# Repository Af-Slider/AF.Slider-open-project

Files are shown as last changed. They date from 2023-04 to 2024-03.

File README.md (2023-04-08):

# AF.Slider-open-project
Open source motorized camera slider, all partes are 3D printable or easy to find on the market. 
Latest version of AF.Slider 21.3

In this repo you can find all the data, files, CAD and scripts used on AF.Slider products. It's distributed under Creative Commons NonCommercial license: feel free to modify and/or change any aspect of the slider, as long as it is used for personal purposes only, without the possibility of it being redistributed or resold. The design of the slider is protected by European Community Design Rights – unregistered Community design (UCD).

<!DOCTYPE html>

<a rel="license" href="http://creativecommons.org/licenses/by-nc-sa/4.0/">

Slider_cover

Here you can find the complete BOM for the slider, together with a sourcing list:

  BOM - https://docs.google.com/spreadsheets/d/e/2PACX-1vTk2jxu348yVe4P4dr0VMHoAVMZ_PHeQANC6IF_kKDuW8Oi32bRA98299qZgVoONA/pubhtml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
  
  Sorucing List - https://docs.google.com/spreadsheets/d/e/2PACX-1vTk2jxu348yVe4P4dr0VMHoAVMZ_PHeQANC6IF_kKDuW8Oi32bRA98299qZgVoONA/pubhtml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

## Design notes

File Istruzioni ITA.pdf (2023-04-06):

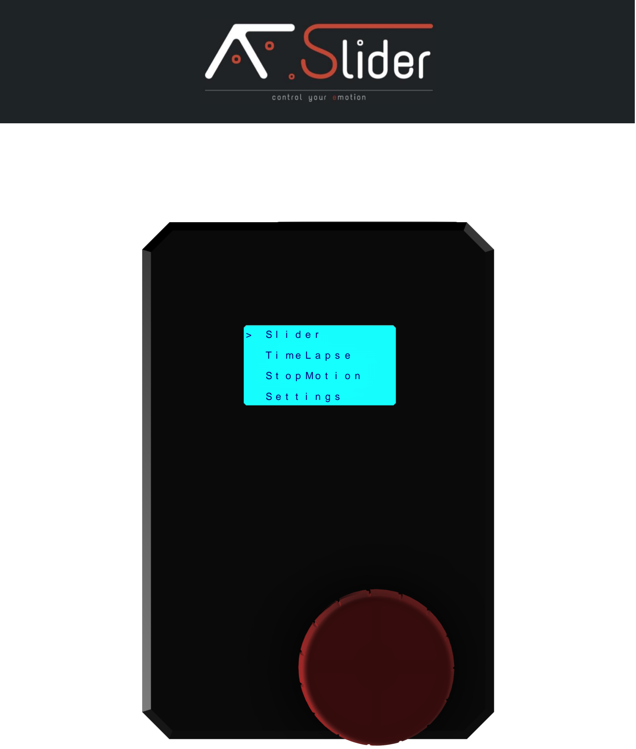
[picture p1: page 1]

> | S l i d e r
| T i m e L a p s e
| S t o p M o t i o n
| S e t t i n g s

# Istruzioni

### Sommario

Componenti dello slider | 3
Primo avvio | 4
Alimentazione | 4
Menu principale | 5
Slider | 5
TimeLapse | 6
StopMotion | 6
Settings | 7
Funzioni Generali | 8
Homing | 8
Firmware Update | 8
Bluetooth e App | 10
Sostituzione dei binari | 11

# Componenti dello slider

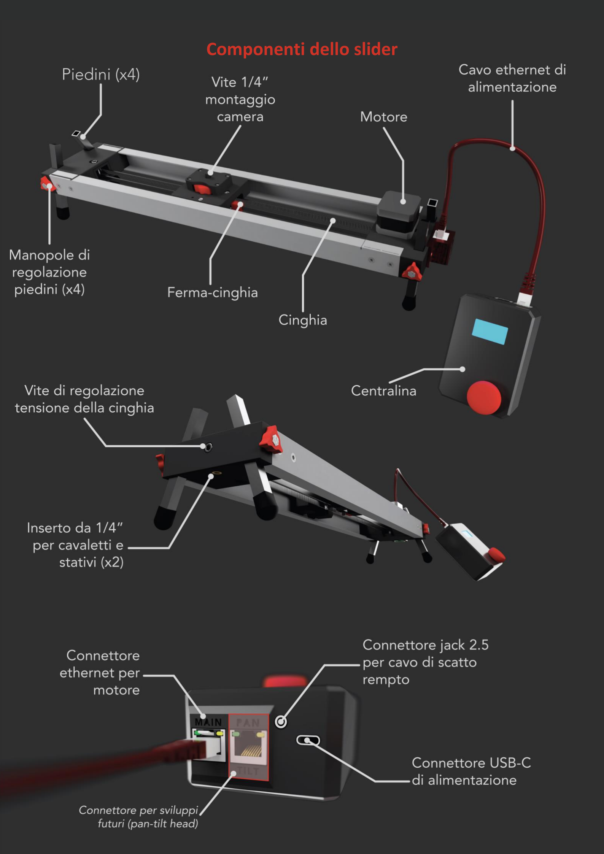
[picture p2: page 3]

# Primo avvio

Prima di avviare lo slider è bene conoscere come connettere correttamente i diversi cavi. All’interno della confezione troverete:
- Un cavo ethernet
- Un cavo USB type-C
- Un alimentatore USB type-C Power Delivery da muro

Cavo USB type-C
Il cavo USB type-C è utilizzato per alimentare lo slider. Connetterlo all’alimentatore fornito in dotazione, o ad altri con caratteristiche simili. È possibile inoltre alimentare lo slider con powerbank purché dotati di presa USB type-C è di tecnologia Power Delivery (per erogare 12V).

Cavo Ethernet
Il cavo ethernet è utilizzato per portare l’alimentazione dalla centralina al motore.
N.B. Assicuratevi di connettere il cavo ethernet alla porta corretta, cioè la porta sulla centralina con dicitura “MAIN”.

N.B. Prima di connettere il cavo di alimentazione dello slider, verificare che il cavo ethernet del motore sia connesso!

Ad ogni accensione lo slider esegue una rapida procedura di calibrazione, cioè verifica la lunghezza dei binari e la posizione di partenza (“HOME”). Durante la procedura di calibrazione, sullo schermo della centralina compare la scritta “homing”. Al termine della procedura, è possibile iniziare ad utilizzare lo slider. Se la procedura di calibrazione non dovesse andare a buon fine, è possibile eseguirla nuovamente dal menu “settings” (vedi capitolo dedicato). N.B. Per garantire la riuscita della procedura di calibrazione, è bene che essa venga eseguita a slider “scarico”, cioè senza che la camera da presa sia montata su di esso.

Cavo jack 2.5” – scatto remoto
Il cavo di scatto remoto deve essere acquistato separatamente e deve essere scelto in base alla camera che verrà utilizzata; il circuito di controllo all’interno della camera infatti è differente per ogni marchio (es. Lumix, SONY, Canon, Nikon, Fujifilm, etc.).
N.B. Per poter utilizzare la funzione di scatto remoto, la camera da presa deve essere impostata su “messa a fuoco manuale”.
Connettere il cavo di scatto remoto con il jack da 3 poli all’interno dell’apposita presa sulla centralina e l’altro capo nel connettore della camera da presa.

# Alimentazione

Per alimentare correttamente lo slider, è bene utilizzare l’alimentatore fornito in dotazione o alimentatori/powerbank con caratteristiche simili:
- Presa USB type-C
- Tecnologia Power Delivery (output 5V, 9V, 12 V)
- 15 W di potenza minima in uscita
Se alimentando lo slider con alimentatori e/o powerbank differenti notate malfunzionamenti o un calo nella forza esercitata dal motore, verificate che l’alimentazione che state utilizzando sia corretta.

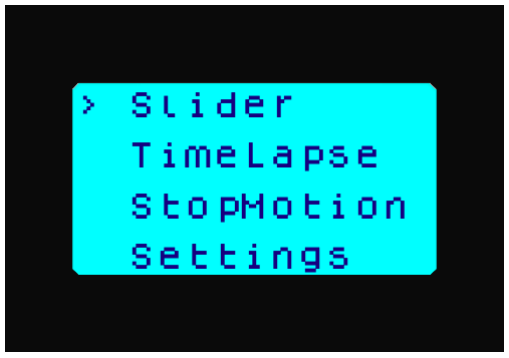
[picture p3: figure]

# Menu principale

Seleziona una delle funzioni presenti per entrare nel sotto-menu relativo.
Per muoversi all’interno del menu, rotare in senso orario o antiorario la manopola presente sulla centralina.
In tutti i menu sono presenti due tipi di cursore:
> | Indica la voce su cui è posizionato il selettore
* | Indica che è stata selezionata la voce ed è possibile modificarne il valore ruotando la manopola

## Slider

Funzione base per poter muovere lo slider con movimento continuo. Ogni cambio di movimento (partenza, stop, ripartenza, etc.) sarà accompagnato da una graduale accelerazione/decelerazione, in base al valore impostato. Di default alla fine del loop lo slider ripeterà il movimento in direzione opposta a ciclo continuo. Per modificare questo parametro vedi il sotto-menu “Settings”.

Speed | velocità a cui si muoverà lo slider (in mm/s)

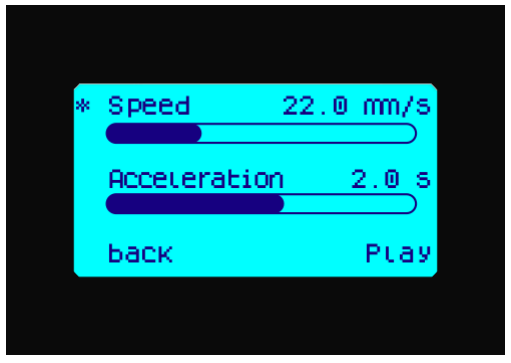
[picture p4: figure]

Acceleration | tempo in secondi che lo slider impiegherà per raggiungere la velocità impostata

## TimeLapse

Permette di muovere lo slider in modo discontinuo e automatico per realizzare timelapse. La camera può essere collegata alla centralina tramite apposito cavo; ad ogni step la centralina muoverà il carrello dello step impostato ed invierà alla camera il comando di scatto remoto. Arrivato a fine corsa lo slider ripeterà la corsa in direzione opposta a ciclo continuo.
Per modificare questo parametro vedi il sotto-menu “Settings”.
Step | Spostamento eseguito ad ogni scatto.

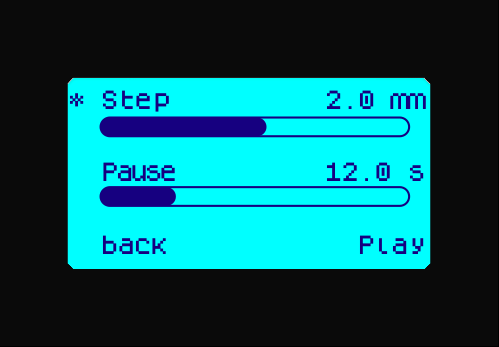
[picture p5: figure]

Pausa | tempo in secondi che lo slider farà intercorrere fra uno scatto ed il successivo
N.B.
La camera deve essere impostata su messa a fuoco manuale per poter scattare in remoto

## StopMotion

Simile alla funzione TimeLapse, ma il movimento ad ogni step avviene solo dopo aver ricevuto il comando dell’operatore. Se la camera è collegata, ad ogni step verrà inviato il comando di scatto remoto. È possibile avanzare ed arretrare di uno step alla volta per eseguito un nuovo scatto o per ripetere il precedente. Arrivato a fine corsa lo slider ripeterà la corsa in direzione opposta a ciclo continuo. Per modificare questo parametro vedi il sotto-menu “Settings”.
N.B.
La camera deve essere impostata su messa a fuoco manuale per poter scattare in remoto

Menu parametri
Step Spostamento eseguito ad ogni scatto.

Menu Play
Next | Esegue uno spostamento in avanti (in direzione del movimento corrente) ed invia il
| comando di scatto remoto alla camera

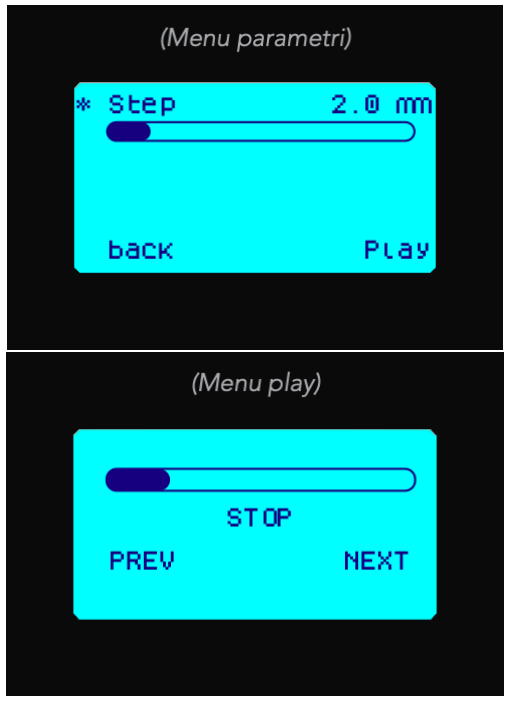
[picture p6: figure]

Prev | Esegue uno spostamento indietro (in direzione opposta al movimento corrente) ed invia il
| comando di scatto remoto alla camera

# Settings

All’interno di questo sotto-menu è possibile cambiare alcune impostazioni generali ed eseguire operazioni particolari:

Impostazione parametri:

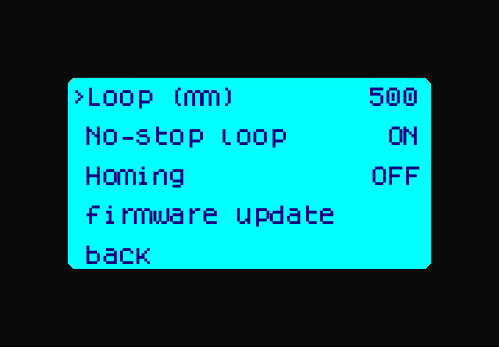
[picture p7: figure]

Loop | Imposta la lunghezza della corsa che deve eseguire lo slider. Di default viene riportata la lunghezza misurata all’avvio dello slider (vedi “homing”). Modificando questo parametro è possibile accorciare la corsa che lo slider esegue per ogni ciclo.
No-stop loop | Se impostato su “ON”, lo slider esegue la corsa in modo continuo “andata” e “ritorno”, senza mai fermarsi. Se impostato su “OFF”, una volta arrivato a fine corsa lo slider si fermerà automaticamente.

Operazioni eccezionali:

Homing | Quando avviato (impostando il valore su “ON”, per evitare di premere accidentalmente la funzione) viene eseguita nuovamente la misurazione dei binari e il posizionamento iniziale (“home”).

Firmware update Permette di aggiornare il firmware. Una volta entrati nel sotto-menu, lo slider
| tenterà di connettersi alla rete Wi-Fi impostata, per registrare l’indirizzo IP a cui effettuare la connessione per eseguire l’aggiornamento. Per eseguire l’aggiornamento vedere la sezione “Firmware Update”.

# Funzioni Generali

### Homing

All’avvio dello slider viene eseguita di default per determinare la lunghezza dei binari e la posizione di partenza (definita “home”). Per garantire il corretto funzionamento di questa operazione è bene che sia eseguita a slider “scarico”, cioè senza camera montata su di esso, in particolar modo se l’operazione viene eseguita quando lo slider è in posizione verticale o inclinata.
È possibile eseguire manualmente questa operazione andando nel sotto-menu “Settings”.

Inoltre è possibile riportare in posizione “home” lo slider in qualsiasi momento (purché lo slider sia fermo), tenendo premuta la manopola per più di 2,5 secondi; al rilascio, lo slider tornerà automaticamente in posizione iniziale.

### Firmware Update

È possibile eseguire l’aggiornamento del firmware qualora dov’esse essere rilasciata una nuova versione. Per eseguire l’aggiornamento, è necessario disporre di:
- Un computer
- Uno smartphone in grado di creare un hotspot
- Una connessione ad internet

Una volta scaricato il file dal sito www.afslider.it, eseguire i seguenti passaggi:

1. Creare una rete Wi-Fi hotspot con il proprio smartphone con le seguenti credenziali (rispettando le maiuscole/minuscole)
a. Nome hotspot – Slider_wifi
b. Password hotspot – Afslider
2. Accedere al sotto-menu “firmware update” (“Settings → firmware update”)
3. Attendere la connessione dello slider alla rete appena creata. Una volta che avrà eseguito l’accesso, sulla schermata comparirà una nuova schermata che riporta la versione corrente del firmware installato e l’indirizzo IP acquisito. Copiare l’indirizzo IP riportato nella schermata.

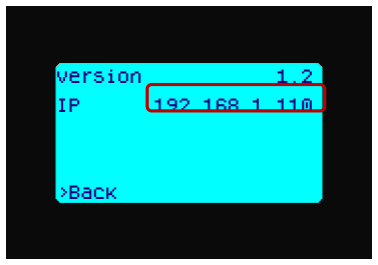
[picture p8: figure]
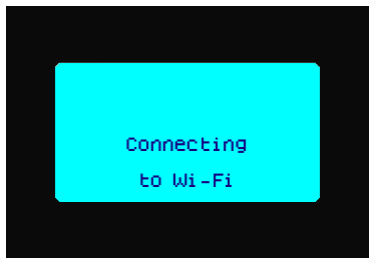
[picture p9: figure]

4. Aprire il browser preferito dal proprio computer (es. Chrome, Firefox, Safari, etc.), ed inserire nella barra di navigazione l’indirizzo IP copiato seguito da “/update”; nell’esempio riportato nell’immagine, verrà digitato -192.168.1.110/update
5. Una volta caricata la schermata, apparirà a schermo la seguente finestra -

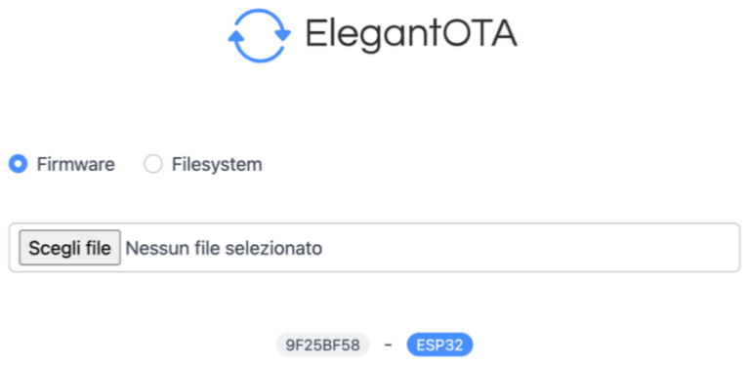
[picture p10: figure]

6. Senza cambiare i parametri già settati di default, selezionare il firmware precedentemente scaricato cliccando su “scegli file”.
7. Il firmware verrà caricato automaticamente. Attendere il completamento della barra di caricamento prima di chiudere la finestra di navigazione.
8. Una volta che l’aggiornamento è stato completato, si noterà che la centralina dello slider si è riavviata. La procedura è quindi conclusa.

Note:
- Se la procedura di upload del firmware allo slider dovesse bloccarsi, spegnere e riaccendere lo slider e ripetere nuovamente la medesima procedura.
- Se dovesse sussisterete il problema, provare ad alimentare la
centralina con un cavo USB-A / USB-C (vedi immagine a lato); così facendo lo slider viene alimentato a 5V anziché a 12V, disattivando alcuni componenti che potrebbero interferire con la procedura di caricamento del firmware.

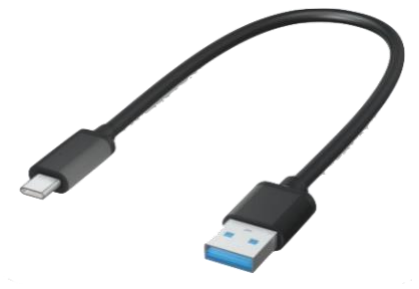
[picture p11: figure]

# Bluetooth e App

Lo slider è già abilitato alla connessione Bluetooth. Su specifica richiesta del cliente è possibile riceve una versione beta dell’applicazione da poter testare. Appena la versione finale dell’applicazione sarà disponibile, tutti gli acquirenti verranno prontamente informati.

Attenzione! La versione beta non garantisce il corretto funzionamento in tutte le circostanze, e può richiedere il riavvio dello slider per ripristinare le funzioni primarie.

# Sostituzione dei binari

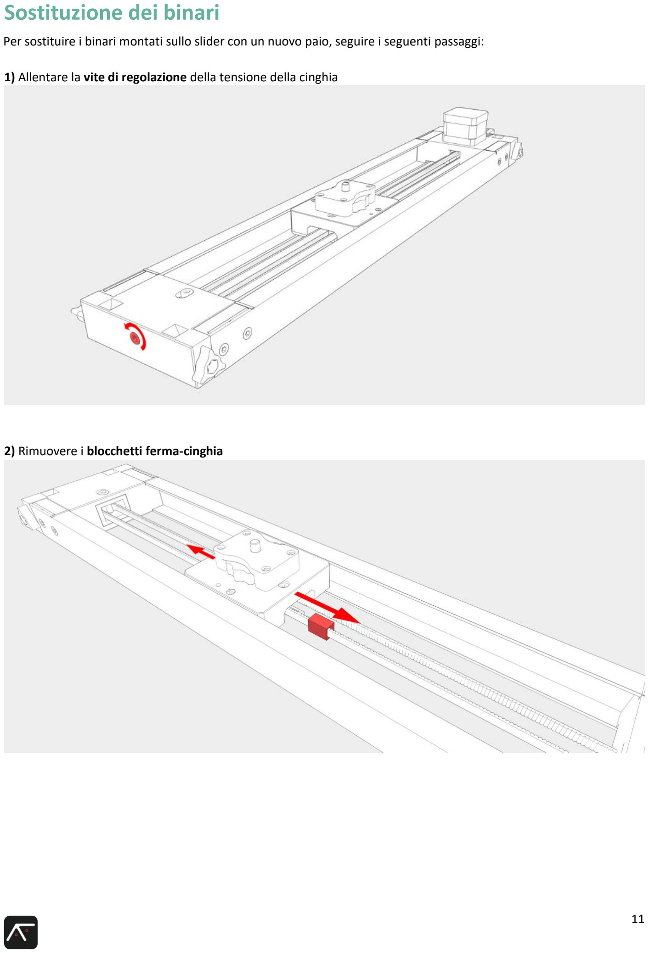
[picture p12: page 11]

Per sostituire i binari montati sullo slider con un nuovo paio, seguire i seguenti passaggi:

1) Allentare la vite di regolazione della tensione della cinghia
2) Rimuovere i blocchetti ferma-cinghia

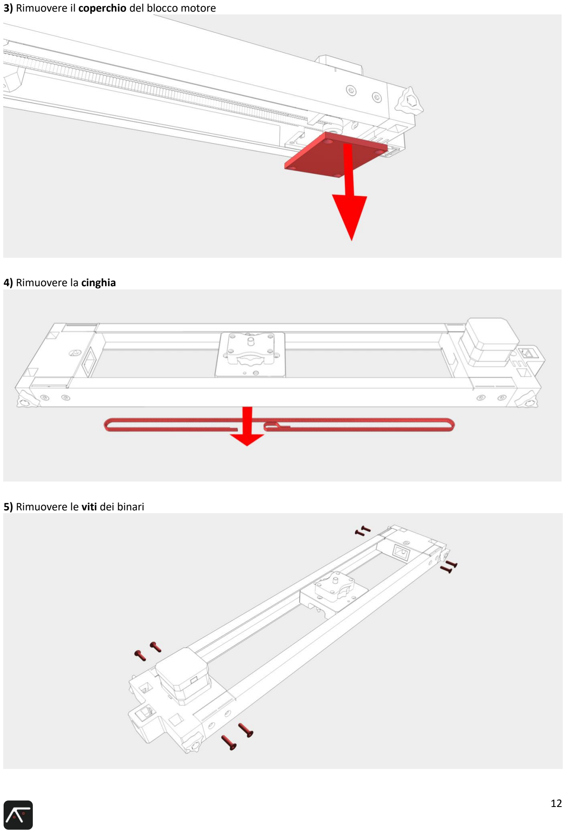
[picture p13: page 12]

3) Rimuovere il coperchio del blocco motore
4) Rimuovere la cinghia
5) Rimuovere le viti dei binari

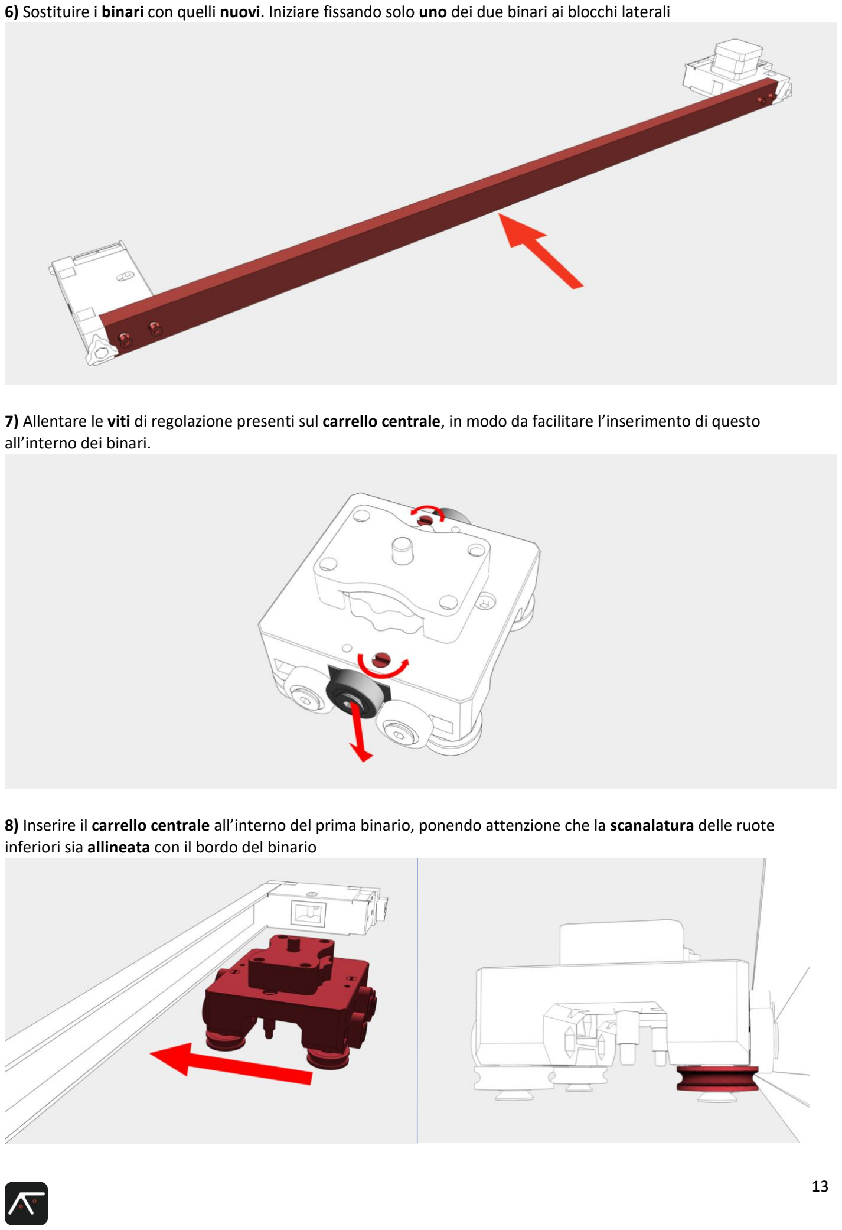
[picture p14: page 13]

6) Sostituire i binari con quelli nuovi. Iniziare fissando solo uno dei due binari ai blocchi laterali
7) Allentare le viti di regolazione presenti sul carrello centrale, in modo da facilitare l’inserimento di questo all’interno dei binari.
8) Inserire il carrello centrale all’interno del prima binario, ponendo attenzione che la scanalatura delle ruote inferiori sia allineata con il bordo del binario

10) Montare il secondo binario, ponendo sempre attenzione che le ruote inferiore del carrello siano ben allineate.

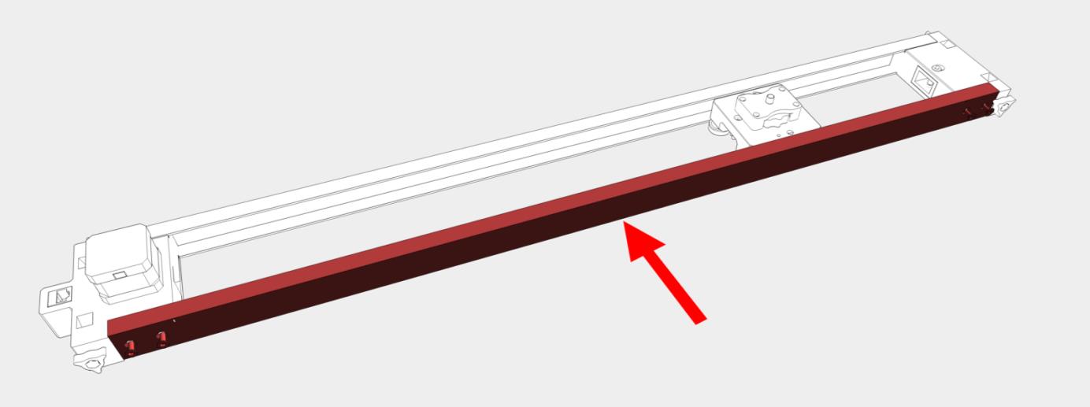
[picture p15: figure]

11) Regolare la posizione delle ruote del carrello centrale con le apposite vite di regolazione. Il carrello deve scorrere senza fare forza, ma senza avere possibilità di muoversi in direzione laterale. Più le viti sono serrate, meno il carrello può muoversi in direzione laterale, ma maggiore sarà la forza richiesta per spostarlo; una forza eccessiva può portare ad un movimento poco fluido del carrello.

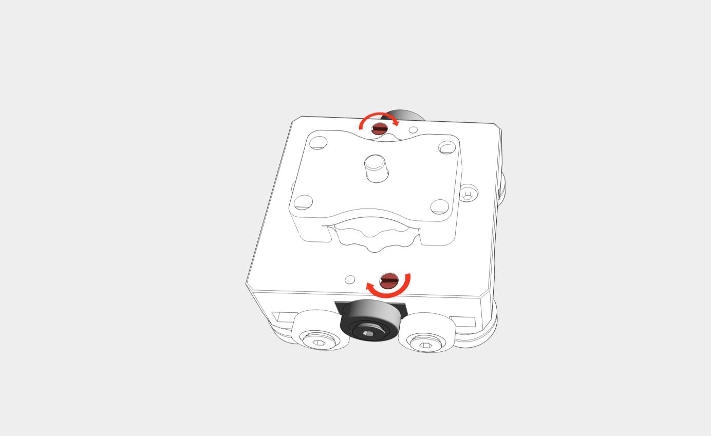
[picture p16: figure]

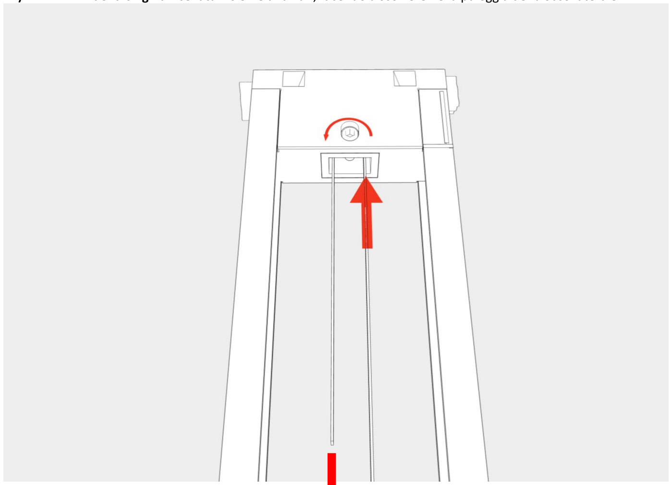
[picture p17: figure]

12) Inserire la nuova cinghia ricevuta insieme ai binari, facendola scorrere nella puleggia del blocco laterale

13) Fissare la cinghia al carrello centrale con i blocchetti ferma-cinghia:
a) Inserire il blocchetto ferma-cinghia sul primo capo della cinghia
b) Fare un’asola attorno al supporto sul carrello centrale con la cinghia stessa
c) Far combaciare le dentature dei due lati opposti della cinghia una volta completata l’asola
d) Far scorrere il blocchetto ferma-cinghia verso l’asola per bloccare la cinghia stessa

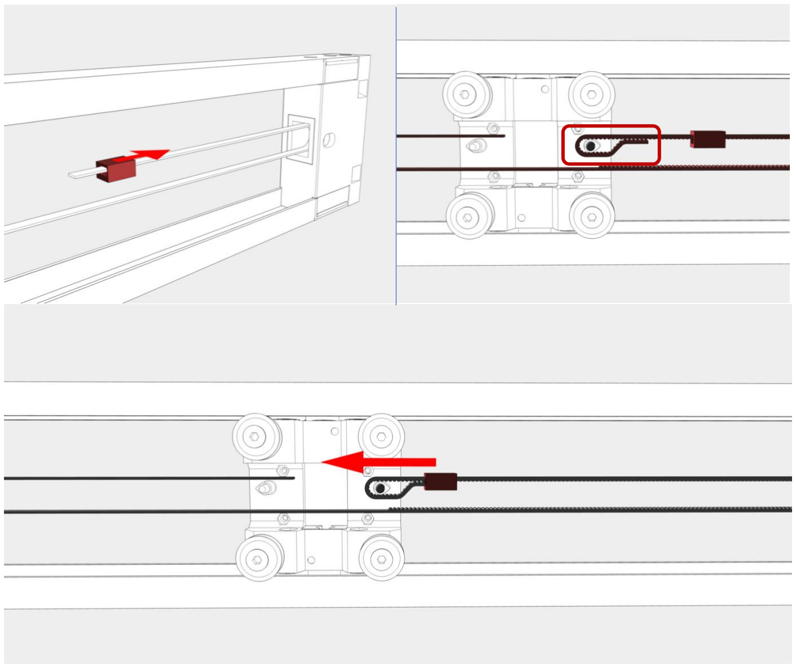
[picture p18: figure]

14) Far scorrere la cinghia attorno alla puleggia del motore

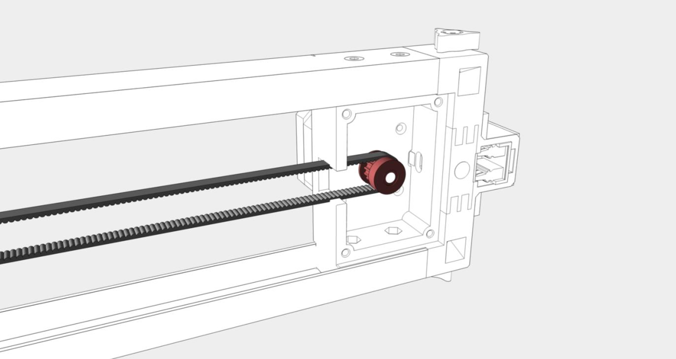
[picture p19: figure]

15) Ripetere le operazioni del passaggio 13 per l’altro capo della cinghia. Prestare attenzione che la cinghia sia sufficientemente tesa prima di fermarla con l’apposito blocchetto ferma-cinghia.
16) Regolare la tensione della cinghia stringendo la vite di regolazione della tensione sul blocco laterale. Verificare che la cinghia non sia troppo tesa facendo scorrere il carrello centrale; se la tensione è corretta si deve sentire una leggera resistenza ma non eccessiva.

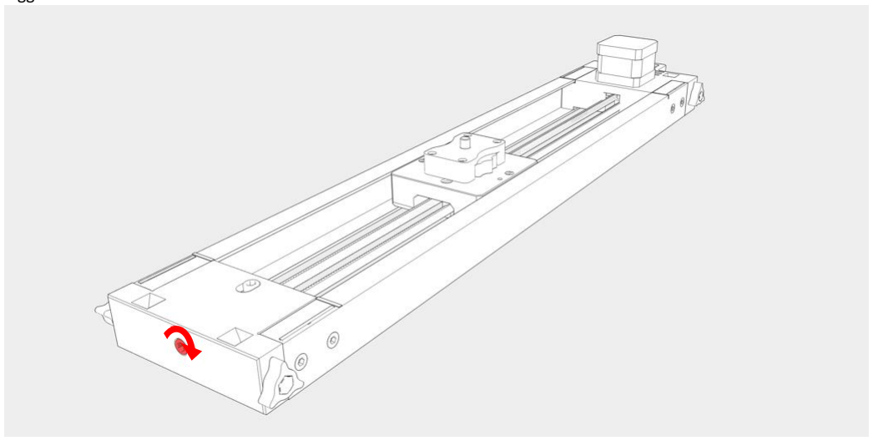
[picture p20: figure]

17) Chiudere il blocco motore con il coperchio.

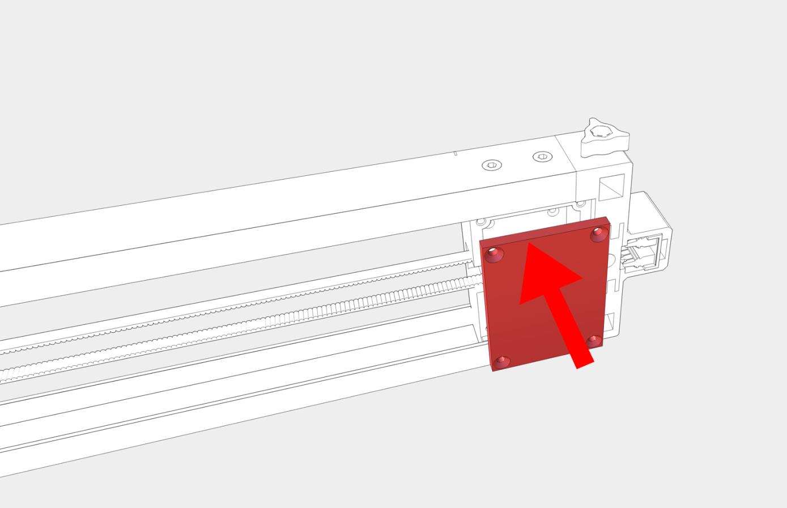
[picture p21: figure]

Avete concluso la procedura! Testate lo slider un paio di volte per verificare che la tensione della cinghia e la posizione delle ruote del carrello centrale sia corretta.

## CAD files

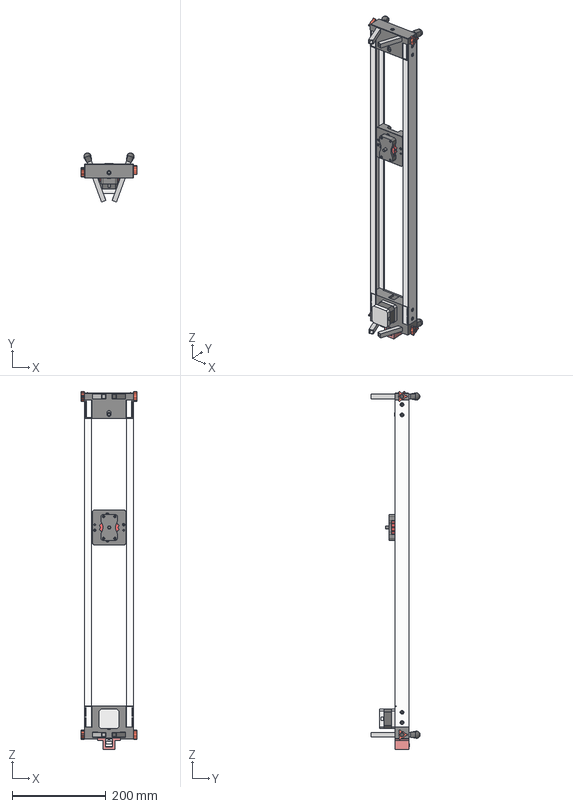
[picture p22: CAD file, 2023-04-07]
CAD/STEP/Assieme Slider V3.4 v84.step
119.8 x 105.1 x 765.7 mm
Profilo_Al x 2
Nema_17_stepper
Coperchio
Keystone_socket_RJ45
T5 Pulley_1
Cuscinetto piatto_crie ruote x 6
Supporto camera V2
Manopola vite 1/4 V2 - wurth
vite 1/4" - 20 x 5/8"
M3 x 6
M5 x 6
M4x 20 svasata x 10
Blocco_laterale
Piedino Al x 4
piedino x 4
M5 Cilindrica x 2
manopola piedini v2 x 4
M5 esagonale x 4
Inserto 1/4"

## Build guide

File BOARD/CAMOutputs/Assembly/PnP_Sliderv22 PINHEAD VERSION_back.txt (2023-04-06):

9V_PAD2	86.11	8.13	180.00		SMD1,27-2,54
GND_PAD2	86.11	3.05	180.00		SMD1,27-2,54

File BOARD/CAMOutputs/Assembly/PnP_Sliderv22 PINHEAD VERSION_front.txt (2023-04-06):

GND	4.83	12.32	90.00		SMD2,54-5,08
PAD1	80.65	3.05	90.00		SMD2,54-5,08
PAD2	80.65	8.13	90.00		SMD2,54-5,08
VCC	4.70	18.41	90.00		SMD2,54-5,08

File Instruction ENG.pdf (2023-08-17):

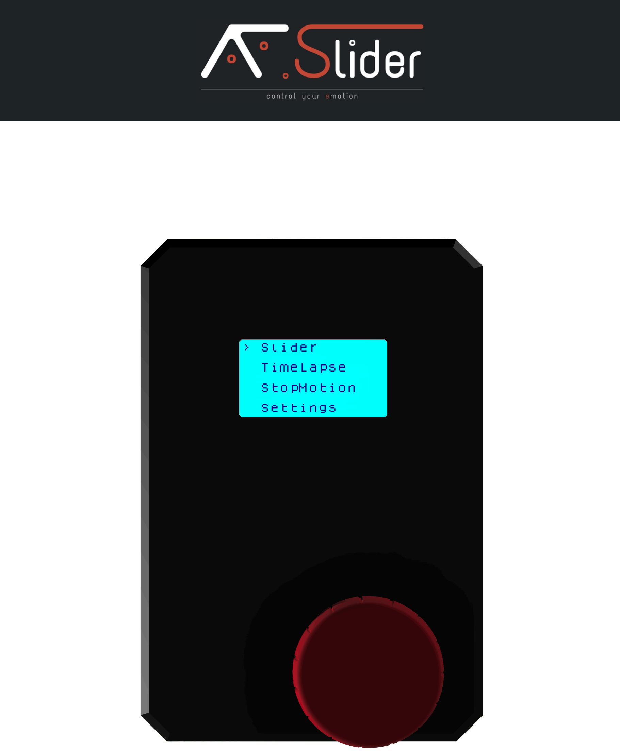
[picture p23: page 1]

> Slider

TimeLapse

StopMotion

Settings

# Instructions

### Summary

Componenti dello slider | 3
Primo avvio | Errore. Il segnalibro non è definito.
Alimentazione | Errore. Il segnalibro non è definito.
Menu principale | 5
Slider | 5
TimeLapse | 6
StopMotion | 6
Settings | 6
Funzioni Generali | 8
Homing | 8
Firmware Update | 8
Bluetooth e App | 10
Sostituzione dei binari | 11

# Slider components

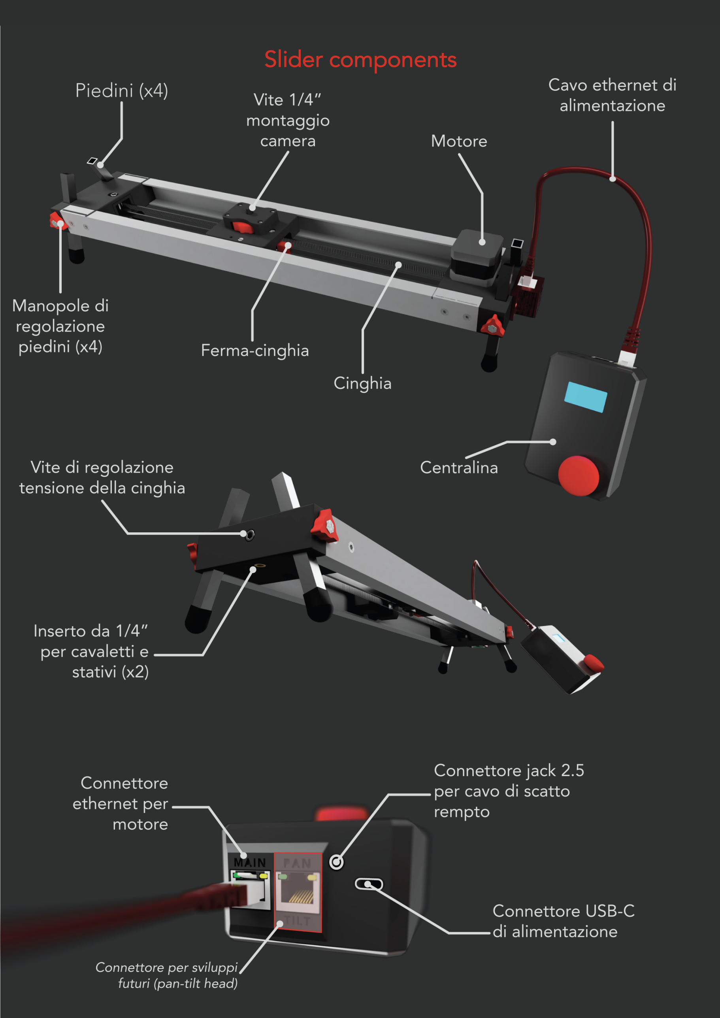
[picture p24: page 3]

# First startup

Before starting the slider, it is good to know how to properly connect the different cables. Inside the package, you will find:
- An Ethernet cable
- A USB Type-C cable
- A USB Type-C Power Delivery wall charger

USB type-C cable
The USB Type-C cable is used to power the slider. Connect it to the provided wall charger or other similar chargers. It is also possible to power the slider with a power bank as long as it has a USB Type-C port and Power Delivery technology (to deliver 12V).

Ethernet cable
The Ethernet cable is used to supply power from the controller to the motor. Note: Make sure to connect the Ethernet cable to the correct port, which is the one labeled "MAIN" on the controller.

Note: Before connecting the power cable to the slider, make sure that the motor's Ethernet cable is connected!

During each power-on, the slider performs a quick calibration procedure to verify the length of the rails and the starting position ("HOME"). During the calibration procedure, the "homing" message appears on the controller's screen. Once the procedure is completed, you can start using the slider. If the calibration procedure fails, you can perform it again from the "settings" menu (refer to the dedicated chapter). Note: To ensure a successful calibration procedure, it is recommended to perform it with the slider "unloaded," meaning without the camera mounted on it.

jack 2.5” Cable – remote shutter

The remote shutter cable needs to be purchased separately and should be chosen based on the camera that will be used. The control circuit inside the camera varies for each brand (e.g., Lumix, SONY, Canon, Nikon, Fujifilm, etc.).
Note: To use the remote shutter function, the camera must be set to "manual focus" mode. Connect the remote shutter cable with the 3-pole jack into the dedicated socket on the controller, and the other end into the camera's connector.

# Power Supply

To properly power the slider, it is recommended to use the provided power adapter or power supplies/power banks with similar specifications:
- USB Type-C port
- Power Delivery technology (output 5V, 9V, 12V)
- Minimum 15W power output
If you experience malfunctions or a decrease in motor force when using different power supplies or power banks, verify that the power source you are using is correct.

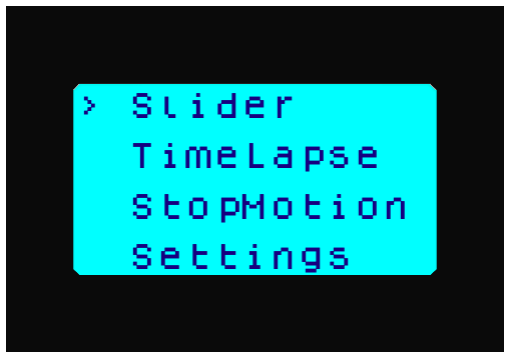
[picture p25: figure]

# Main Menu

Choose one of the available functions to access the corresponding submenu. To navigate within the menu, rotate the dial on the controller clockwise or counterclockwise. In all menus, you will find two types of cursors.

> | It indicate the option on which the selector is positioned
* | It indicates that the option has been selected, and the value can be modified by rotating the dial

## Slider

The basic function that allows you to move the slider with continuous motion. Each change of motion (start, stop, restart, etc.) will be accompanied by a gradual acceleration/deceleration, based on the set value. By default, at the end of the loop, the slider will repeat the movement in the opposite direction in a continuous cycle. To modify this parameter, please refer to the "Settings" submenu.

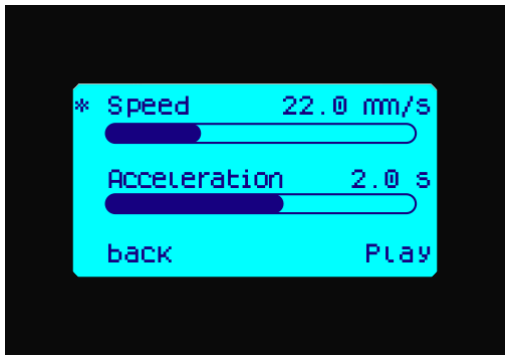
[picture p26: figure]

Speed The speed at which the slider will move is measured in mm/s (millimeters per second).

Acceleration The time in seconds that the slider will take to reach the set speed

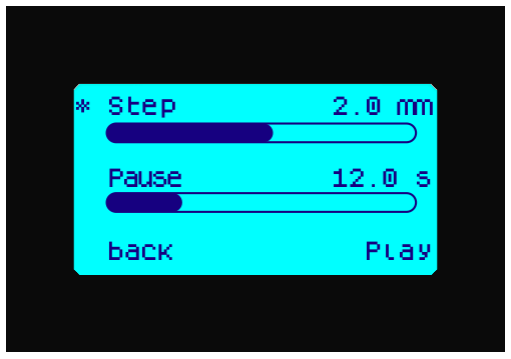
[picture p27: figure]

## TimeLapse

Allows you to move the slider in a discontinuous and automatic manner to create timelapse sequences. The camera can be connected to the controller using a dedicated cable. At each step, the controller will move the slider by the set step distance and send a remote shutter command to the camera. Once it reaches the end of the rail, the slider will repeat the movement in the opposite direction in a continuous cycle. To modify this parameter, refer to the "Settings" submenu.

Step movement that will be performed at each step
Pausa time in second between each step
N.B.
The camera needs to be set to manual focus in order to take remote shots.

## StopMotion

Similar to the TimeLapse function, but the movement at each step occurs only after receiving the command from the operator. If the camera is connected, a remote shutter command will be sent at each step. It is possible to move forward and backward one step at a time to take a new shot or repeat the previous one. Once it reaches the end of the rail, the slider will repeat the movement in the opposite direction in a continuous cycle. To modify this parameter, refer to the "Settings" submenu.

N.B.
The camera needs to be set to manual focus in order to take remote shots.

Parameters Menu
Step movement that will be performed at each step

Menu Play

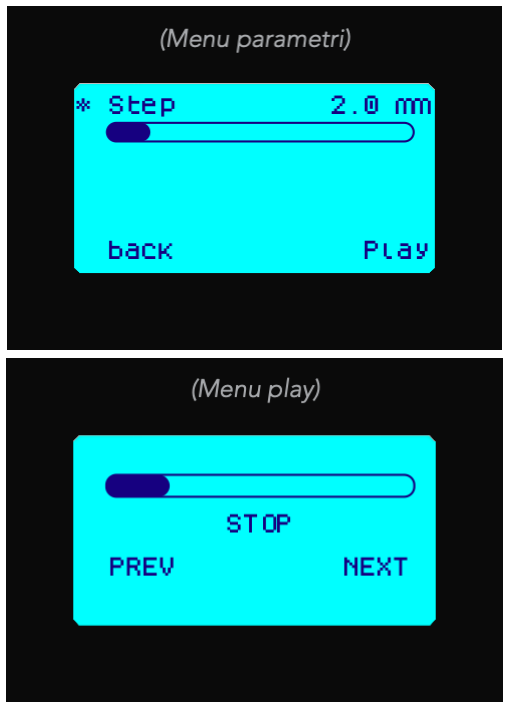
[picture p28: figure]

Next | It performs a forward movement (in the direction of the current motion) and sends the remote
| shutter command to the camera.
Prev | It performs a backward movement (in the opposite direction of the current motion) and sends the
| remote shutter command to the camera.

Settings
Within this submenu, you can change some general settings and perform specific operations.

Parameters set:


Loop | Set the length of the travel that the slider should perform. By default, it displays the length measured during the slider's initialization (refer to "homing"). By modifying this parameter, you can shorten the travel distance that the slider completes in each cycle.
No-stop loop | If set to "ON", the slider will continuously move back and forth without ever stopping. If set to "OFF", once it reaches the end of the rail, the slider will automatically stop.

Exceptional operations:

Homing | When started (by setting the value to "ON" to avoid accidentally triggering the function), the measurement of the rails and the initial positioning ("home") is performed again.
Firmware update | It allows you to update the firmware. Once you enter the submenu, the slider will attempt to connect to the set Wi-Fi network to record the IP address for the connection to perform the update. To carry out the update, refer to the "Firmware Update" section.

# General Functions

### Homing

By default, when the slider is powered on, it performs a calibration procedure to determine the rail length and the starting position, referred to as "home." To ensure the proper functioning of this operation, it is recommended to perform it with the slider "unloaded," meaning without a camera mounted on it, especially if the operation is carried out when the slider is in a vertical or tilted position.
You can manually execute this operation by accessing the "Settings" submenu.
Additionally, it is possible to return the slider to the "home" position at any time (as long as the slider is stationary) by pressing and holding the dial for more than 2.5 seconds. Upon release, the slider will automatically return to its initial position.

### Firmware Update

You can update the firmware if a new version is released. To perform the update, you will need:

- A computer
- A smartphone capable of creating a hotspot
- An internet connection

Once you have downloaded the file from the website www.afslider.it, follow these steps:

1. Create a Wi-Fi hotspot network with your smartphone using the following credentials (pay attention to uppercase/lowercase letters):
a. Hotspot name – Slider_wifi
b. Hotspot password – Afslider
2. Access the "firmware update" submenu ("Settings → firmware update").
3. Wait for the slider to connect to the newly created network. Once it has successfully connected, a new screen will appear displaying the current installed firmware version and the acquired IP address. Copy the displayed IP address.

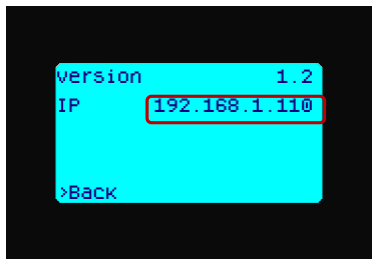
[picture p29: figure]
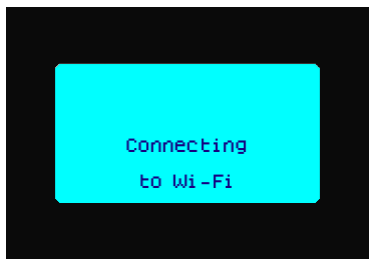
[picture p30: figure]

4. Open your preferred browser on your computer (e.g., Chrome, Firefox, Safari, etc.) and enter the copied IP address followed by "/update" in the navigation bar. In the example shown in the image, it would be typed as -

192.168.1.110/update

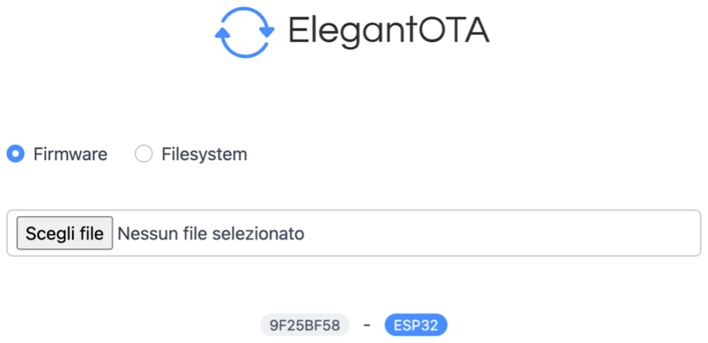
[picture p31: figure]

5. Once the screen is loaded, the following window will appear on the screen.
6. Without changing the default settings, select the previously downloaded firmware by clicking on "choose file."
7. The firmware will be automatically uploaded. Wait for the progress bar to complete before closing the browser window.
8. Once the update is completed, you will notice that the slider's controller has restarted. The procedure is now complete.

Note:
- If the firmware upload process to the slider gets stuck, turn off and restart the slider, then repeat the same procedure.
- If the issue persists, try powering the controller with a USB-A
to USB-C cable (as shown in the image). By doing so, the slider is powered at 5V instead of 12V, deactivating some components that might interfere with the firmware upload process.

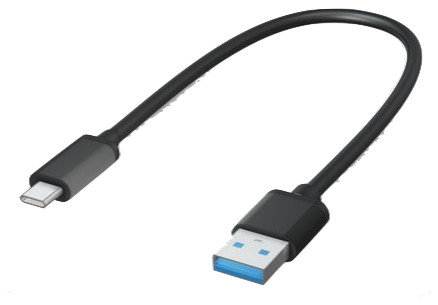
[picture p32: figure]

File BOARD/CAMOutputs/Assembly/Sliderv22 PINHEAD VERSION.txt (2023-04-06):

Partlist exported from /Users/fulvio_airaghi/Documents/EAGLE/projects/Test_project/Sliderv22 PINHEAD VERSION.sch at 07/10/22 12:50

Qty Value          Device                Package      Parts                                Description                     DATASHEET                                                                                                                                                          MANUFACTURER    MF                      MPN  OC_FARNELL OC_NEWARK PARTREV POPULARITY SPICEPREFIX STANDARD                    
6                  1,6/0,8               1,6/0,8      PAD3, PAD6, PAD8, PAD9, PAD12, PAD13 THROUGH-HOLE PAD                                                                                                                                                                                                                                                             15                                                 
2                  2,54/1,0              2,54/1,0     9V_PAD, GND_PAD                      THROUGH-HOLE PAD                                                                                                                                                                                                                                                             1                                                  
1                  FE04-1FE-04-1         FE04-1       SV9                                  FEMALE HEADER                                                                                                                                                                                                                                                                                                                   
3                  FE08-TMC2209-DXFE8-DX FE08-DX      SV1, SV5, SV7                        FEMALE HEADER                                                                                                                                                                                                                                                                                                                   
3                  FE08-TMC2209-SX       FE08-SX      SV4, SV6, SV8                        FEMALE HEADER                                                                                                                                                                                                                                   unknown    unknown           10                                                 
1                  FE15-1-ESP32-DX       FE15-DX      SV3                                  FEMALE HEADER                                                                                                                                                                                                                                                                                                                   
1                  FE15-1-ESP32-SX       FE15-SX      SV2                                  FEMALE HEADER                                                                                                                                                                                                                                                                                                                   
2                  SMD2                  SMD1,27-2,54 9V_PAD2, GND_PAD2                    SMD PAD                                                                                                                                                                                                                                                                      15                                                 
4                  SMD5                  SMD2,54-5,08 GND, PAD1, PAD2, VCC                 SMD PAD                                                                                                                                                                                                                                                                      21                                                 
1   10             R-US_0204/7           0204/7       R2                                   RESISTOR, American symbol                                                                                                                                                                                                                                                    48         R                                       
1   1K             R-US_0204/7           0204/7       R1                                   RESISTOR, American symbol                                                                                                                                                                                                                                                    48         R                                       
1   4N35           4N35                  DIL06        OK1                                  MOTOROLA OPTO COUPLER                                                                                                                                                                                              FAIRCHILD SEMICONDUCTOR 4N35 1328375    72K9946           1                                                  
2   5569564-1      5569564-1             TE_5569564-1 RJ45_MAIN, RJ45_PAN_TILT             CONN MOD JACK 8P8C R/A SHIELDED http://www.te.com/commerce/DocumentDelivery/DDEController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 TE CONNECTIVITY                                                   E2                             Manufacturer Recommendations
2   5K             R-US_0207/12          0207/12      R3, R4                               RESISTOR, American symbol                                                                                                                                                                                                                                                    3          R                                       
1   62P16-H0       62P16-H0              62P          RE2                                                                                                                                                                                                                                                                                                                                                                  
1   JW-PJ-307-5H   JW-PJ-307-5H          JW-PJ-307-5H J2                                                                                                                                                                                                                                                                                                                                                                   
1   WIREPAD1,6/0,9 1,6/0,8               1,6/0,8      PAD10                                THROUGH-HOLE PAD                                                                                                                                                                                                                                                             15

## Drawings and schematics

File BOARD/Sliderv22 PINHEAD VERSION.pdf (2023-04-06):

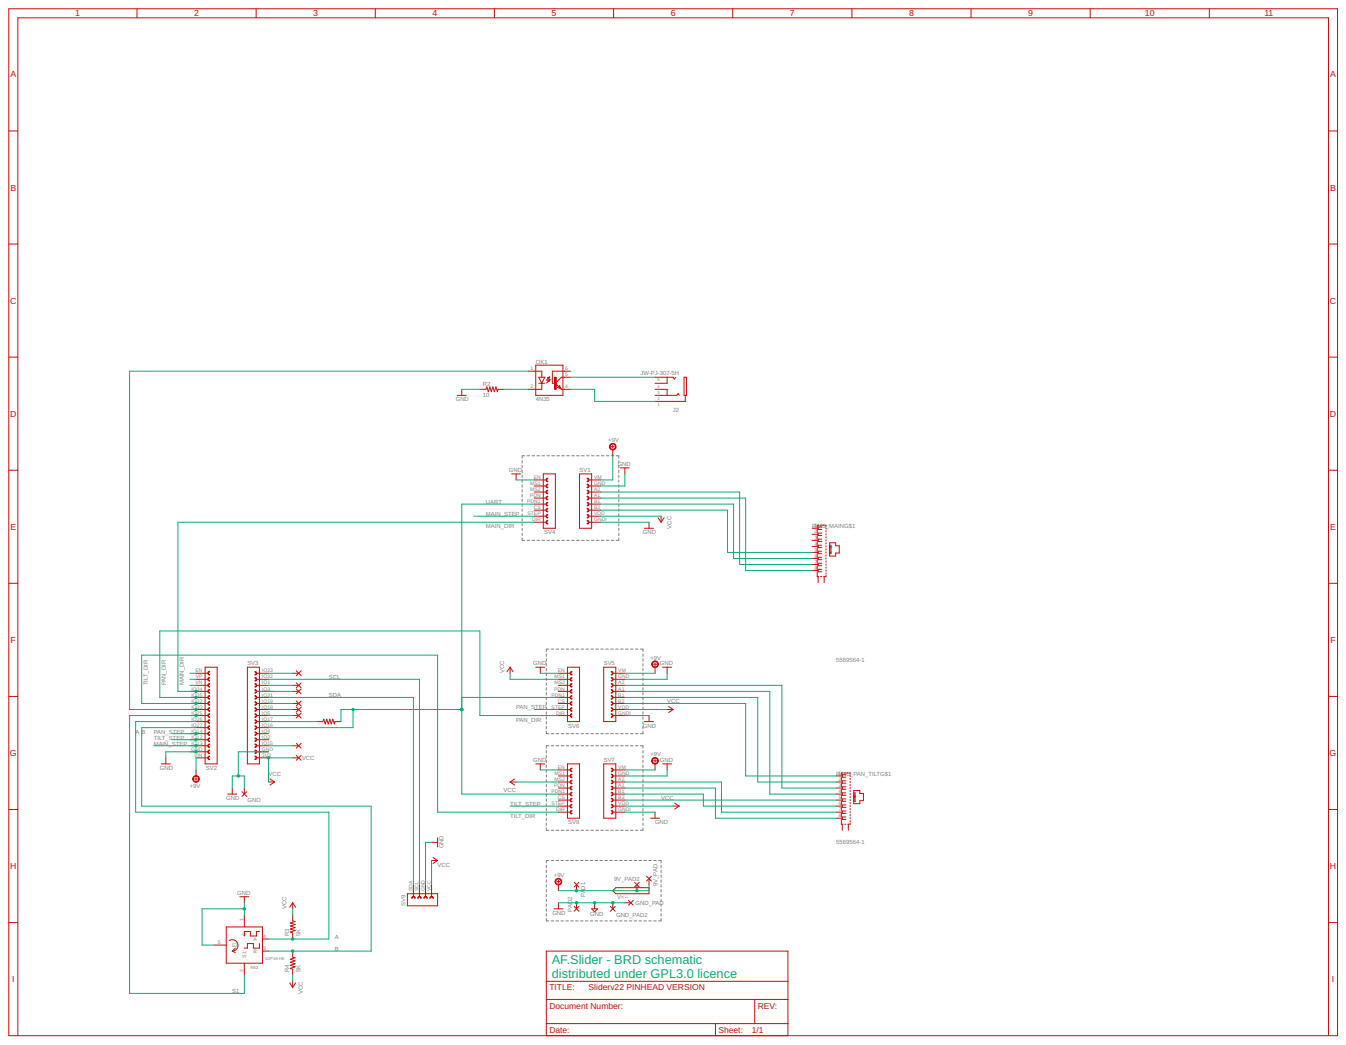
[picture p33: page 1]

AF.Slider - BRD schematic
distributed under GPL3.0 licence
TITLE:

Document Number: | REV:

Date: | Sheet: 1/1

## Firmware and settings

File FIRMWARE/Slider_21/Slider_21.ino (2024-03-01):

/*
 * Firmware developed by Fulvio Airaghi and based on several open source library under MIT licence. 
 * The present code is distributed by MIT licence as well, WITHOUT the permision of commercial use. 
 * 
 * 
 * Firmware version 1.3
 */
#define FW 2.0
#define debugM 0 //1 to enable serial.print, 2 to plot stallGuard value, 0 to disable

#include "OLED_encoder.h"
#include "BLE.h"

unsigned long print_timer;
unsigned int TL_timer;

#if defined(ESP8266)
  #include <ESP8266WiFi.h>
  #include <ESPAsyncTCP.h>
#elif defined(ESP32)
  #include <WiFi.h>
  #include <AsyncTCP.h>
#endif

#include <ESPAsyncWebServer.h>
#include <AsyncElegantOTA.h>

const char* ssid = "Slider_wifi";
const char* password = "Afslider";

AsyncWebServer server(80);

void setup() { 
  
  pulley_diam = 12.20; // diameter of the pulley, in mm
  
  Serial.begin(500000); 


//____________________________________________________________________OTA server
/*
 * Vedi "settings --> Firmware update"
 */

  
//____________________________________________________________________BLE

  BLEDevice::init("AF.Slider");
  BLEServer *pServer = BLEDevice::createServer();

  BLEService *pService = pServer->createService(SERVICE_UUID);

  // Define characteristics for this service, and assign read/write properties
  
  BLECharacteristic *start_stop_Characteristic = pService->createCharacteristic(
                                         start_stop_UUID,
                                         BLECharacteristic::PROPERTY_READ |
                                         BLECharacteristic::PROPERTY_WRITE 
                                         //BLECharacteristic::PROPERTY_NOTIFY
                                       );

  start_stop_Characteristic->setCallbacks(new StartStopCallbacks());
 
  BLECharacteristic *speed_Characteristic = pService->createCharacteristic(
                                         speed_UUID,
                                         BLECharacteristic::PROPERTY_READ |
                                         BLECharacteristic::PROPERTY_WRITE 
                                         //BLECharacteristic::PROPERTY_NOTIFY
                                       );

  speed_Characteristic->setCallbacks(new speedCallbacks());
  
/*
  BLECharacteristic *acc_Characteristic = pService->createCharacteristic(
                                         acc_UUID,
                                         BLECharacteristic::PROPERTY_READ |
                                         BLECharacteristic::PROPERTY_WRITE 
                                         //BLECharacteristic::PROPERTY_NOTIFY
                                       );

  acc_Characteristic->setCallbacks(new accCallbacks());
*/

  BLECharacteristic *step_Characteristic = pService->createCharacteristic(
                                         step_UUID,
                                         BLECharacteristic::PROPERTY_READ |
                                         BLECharacteristic::PROPERTY_WRITE 
                                         //BLECharacteristic::PROPERTY_NOTIFY
                                       );
  step_Characteristic->setCallbacks(new stepCallbacks());
/*
  BLECharacteristic *pause_Characteristic = pService->createCharacteristic(
                                         pause_UUID,
                                         BLECharacteristic::PROPERTY_READ |
                                         BLECharacteristic::PROPERTY_WRITE |
                                         BLECharacteristic::PROPERTY_NOTIFY
                                       );

  pause_Characteristic->setCallbacks(new pauseCallbacks());
*/
  BLECharacteristic *loop_Characteristic = pService->createCharacteristic(
                                         loop_UUID,
                                         BLECharacteristic::PROPERTY_READ |
                                         BLECharacteristic::PROPERTY_WRITE 
                                         //BLECharacteristic::PROPERTY_NOTIFY
                                       );

  loop_Characteristic->setCallbacks(new loopCallbacks());

  /*
  BLECharacteristic *starting_point_Characteristic = pService->createCharacteristic(
                                         starting_point_UUID,
                                         BLECharacteristic::PROPERTY_READ |
                                         BLECharacteristic::PROPERTY_WRITE |
                                         BLECharacteristic::PROPERTY_NOTIFY
                                       );

  starting_point_Characteristic->setCallbacks(new starting_point_Callbacks());
  */
  
  pServer->setCallbacks(new MyServerCallbacks());

  start_stop_Characteristic->setValue("Hello World");
  pService->start();

//  BLEAdvertising *pAdvertising = pServer->getAdvertising();
//  pAdvertising->start();
  BLEAdvertising *pAdvertising = BLEDevice::getAdvertising();
  pAdvertising->addServiceUUID(SERVICE_UUID);
  pAdvertising->setScanResponse(true);
  pAdvertising->setMinPreferred(0x06);  // functions that help with iPhone connections issue
  pAdvertising->setMinPreferred(0x12);
  BLEDevice::startAdvertising();

//____________________________________________________________________OLED & MENU & ENCODER setup
  Slider.title = "Slider";
  Slider.variables[0].title = "speed";
  Slider.variables[0].val = 20;
  Slider.variables[0].maxVal = 105;
  Slider.variables[0].minVal = 0;
  Slider.variables[0].unit = "mm/s";
  Slider.variables[1].title = "acceleration";
  Slider.variables[1].multi = 0.1;
  Slider.variables[1].val = 2.5;
  Slider.variables[1].maxVal = 10;
  Slider.variables[1].minVal = 0.2;
  Slider.variables[1].unit = "s";
  Slider.variables[2].title = "Back";
  Slider.variables[2].val = -1;                              //used to avoid progress bar print
  Slider.variables[3].title = "Play";

  TimeLapse.title = "TimeLapse";
  TimeLapse.variables[0].title = "step";
  TimeLapse.variables[0].multi = 0.1;  
  TimeLapse.variables[0].val = 3;
  TimeLapse.variables[0].maxVal = 400;
  TimeLapse.variables[0].minVal = 0;
  TimeLapse.variables[0].unit = "mm";
  TimeLapse.variables[1].title = "pause";
  TimeLapse.variables[1].multi = 0.1;  
  TimeLapse.variables[1].val = 4.2;
  TimeLapse.variables[1].maxVal = 360;
  TimeLapse.variables[1].minVal = 0;
  TimeLapse.variables[1].unit = "s";
  TimeLapse.variables[2].title = "Back";
  TimeLapse.variables[2].val = -1;
  TimeLapse.variables[3].title = "Play";

  StopMotion.title = "StopMotion";
  StopMotion.variables[0].title = "step";
  StopMotion.variables[0].multi = 0.1;  
  StopMotion.variables[0].val = 3;
  StopMotion.variables[0].maxVal = 400;
  StopMotion.variables[0].minVal = 0;
  StopMotion.variables[0].unit = "mm";
  StopMotion.variables[1].val = -1;                            
  StopMotion.variables[2].title = "Back";
  StopMotion.variables[2].val = -1;
  StopMotion.variables[3].title = "Play";
  
  Settings.title = "Settings";
  Settings.variables[0].title = "Loop"; 
  Settings.variables[0].val = 500;
  Settings.variables[0].maxVal = 1200;
  Settings.variables[0].minVal = 0;
  Settings.variables[0].unit = " (mm)"; 
  Settings.variables[1].title = "No-stop loop";
  Settings.variables[1].val = 1;
  Settings.variables[1].maxVal = 1;
  Settings.variables[1].minVal = 0;
  Settings.variables[2].title = "homing";
  Settings.variables[2].val = 0;
  Settings.variables[2].maxVal = 1;
  Settings.variables[2].minVal = 0;
  Settings.variables[3].title = "Firmware update";
  Settings.variables[4].title = "Back";
  Settings.variables[4].val = -1;

  pinMode (DT, INPUT_PULLUP);
  pinMode (CLK, INPUT_PULLUP);
  pinMode (SW, INPUT_PULLUP);
  pinMode (BT_LED, OUTPUT);
  pinMode (33, OUTPUT);
  
  attachInterrupt(DT, UpdateEncoder, CHANGE);
  attachInterrupt(CLK, UpdateEncoder, CHANGE);
  attachInterrupt(SW, up, FALLING);

  display.flipScreenVertically();
  display.init();

  display.clear();
  display.setTextAlignment(TEXT_ALIGN_CENTER);
  display.setFont(Roboto_Light_12);
  display.drawString(128/2, (64/2 - 12), "AF.Slider");
  display.display();
  delay (1000); 
  
//____________________________________________________________________Stepper
  Serial2.begin(500000);        // SW UART drivers
  
  driver.begin();               // SPI: Init CS pins and possible SW SPI pins
  driver.toff(TOFF_VALUE);      // Sets the slow decay time (off time) [1... 15] --> 0 motor off, enything else motor on
  driver.TCOOLTHRS(0xFFFFF);    // 20bit max - Lower threshold velocity for switching on smart energy CoolStep and StallGuard to DIAG output
  driver.blank_time(24);        // Comparator blank time. This time needs to safely cover the switching event and the duration of the ringing on the sense resistor
  driver.semin(10);             // CoolStep lower threshold [0... 15]. If SG_RESULT goes below this threshold, CoolStep increases the current to both coils.
                                // 0: disable CoolStep
  driver.semax(1);              // CoolStep upper threshold [0... 15]. If SG is sampled equal to or above this threshold enough times,
                                // CoolStep decreases the current to both coils.
  driver.rms_current(stepperCurrent, 0.3);  //RMS current, hold current multiplier, sense resistor value - (required, optional, optional)
  driver.microsteps(MICROSTEPS);
  driver.sedn(0b101);           // Sets the number of StallGuard2 readings above the upper threshold necessary for each current decrement of the motor current
  
  driver.SGTHRS(STALL_VALUE);  // StallGuard4 threshold [0... 255] level for stall detection.
                                // A higher value gives a higher sensitivity. A higher value makes StallGuard4 more sensitive and requires less torque to
                                // indicate a stall.

  engine.init();
  stepper = engine.stepperConnectToPin(stepPinStepper);
  if (stepper) {
    stepper->setDirectionPin(dirPinStepper, 0, 0); //setDirectionPin(uint8_t dirPin, bool dirHighCountsUp, uint16_t dir_change_delay_us)
    stepper->setEnablePin(enablePinStepper);
    stepper->setAutoEnable(true);

    stepper->setSpeedInUs(homing_speed);  // the parameter is us/step !!!
    stepper->setAcceleration(homing_speed); // the parameter is steps/s²
  }
  
//___________________________________________________________________test driver comunication

  if (debugM) Serial.println(F("\nTesting connection..."));
  uint8_t result = driver.test_connection();

  if (result) {
    if (debugM) Serial.println("failed!");
    if (debugM) Serial.print("Likely cause: ");

    switch(result) {
        case 1: if (debugM) Serial.println("loose connection"); break;
        case 2: if (debugM) Serial.println("no power"); break;
    }
    if (debugM) Serial.println("Fix the problem and reset board.");

    // We need this delay or messages above don't get fully printed out
    delay(100);
    //abort();
    //while (1);
  }
  if (debugM) Serial.println("OK");

  
//___________________________________________________________________Homing routine

  delay(500);

  direction = 0;
  driver.shaft(!direction);
  
  if (debugM) Serial.println(F("start homing"));
  homing();
  
  if (debugM) Serial.println(F("fine homing"));
  if (debugM) Serial.print(F("current Position: "));
  if (debugM) Serial.println(stepper->getCurrentPosition());

  assignVal();
  delay(200);
  
  stepper->setAcceleration(1000);
  stepper->setSpeedInUs(600); 
  direction = 1;
  driver.shaft(direction);
  stepper->moveTo(HOME, 1);
  Settings.variables[2].val = 0;
  
  if (debugM) Serial.print(F("steps tot: "));
  if (debugM) Serial.println(END);
  if (debugM) Serial.print(F("lunghezza loop: "));
  if (debugM) Serial.println(Settings.variables[0].val);

  double temp = Settings.variables[0].val;
  char txString[8];
  dtostrf(temp, 1, 2, txString);

  loop_Characteristic->setValue(txString);

  timing = millis();
  input_speed = Slider.variables[0].val;
  conversion();
  
}//___________________________________________________________________end setup


void loop() {

  if (updateData) {
    OLED_print();
    assignVal();
    updateData = false;
  }

  if (start_wifi){
    if (WiFi.status() != WL_CONNECTED) firmware_update();
  }

  if (goingHome && stepper->getCurrentPosition() != HOME){
    display.clear();
    display.setTextAlignment(TEXT_ALIGN_CENTER);
    display.drawString(128/2, (64/2 - 12), "going home");
    display.display();  
    goingHome = false;
    delay(1000);
    OLED_print();
  }

  if (revaluate && play){
    bool store_direction = direction;
    max_frame = floor (END / TL_steps);
    if (direction = 0 && frame_count != 0) frame_count = floor (stepper->getCurrentPosition() / TL_steps) - 1;
    else if (frame_count != 0) frame_count = ceil (stepper->getCurrentPosition() / TL_steps) - 1;
    int prevPos = TL_steps * frame_count;
    driver.shaft(!direction);
    stepper->moveTo(prevPos,1);
    direction = store_direction;
    driver.shaft(direction);
    delay(50);
    revaluate = false;
  }
  
  if (play){

    int selector;

    if ( menuList[functionMenuSel]->title == "Slider" ) selector = 0;
    if ( menuList[functionMenuSel]->title == "TimeLapse" ) selector = 1;
    if ( menuList[functionMenuSel]->title == "StopMotion" ) selector = 2;
    if ( menuList[functionMenuSel]->title == "Settings" ) selector = 3;

    max_frame = floor (END / TL_steps);
    if (selector == 1){
      if (stepper->getCurrentPosition() != 0 && frame_count == 0) frame_count = floor (stepper->getCurrentPosition() / TL_steps);
    }
    switch (selector){
      
      // Slider
      case 0: 
      if (stepper->getCurrentPosition() == END) direction = 1; 
      else if (stepper->getCurrentPosition() == HOME) direction = 0; 
      driver.shaft(direction);
      
        if (run_cont){
          if (!stepper->isRunning()){
            if (direction) stepper->moveTo(HOME);
            else stepper->moveTo(END);
          }
        }
        else {
          if (direction) {
            stepper->moveTo(HOME);
            if (stepper->getCurrentPosition() == HOME) play = false, layer = 1, OLED_print();
          }
          else {
            stepper->moveTo(END);
            if (stepper->getCurrentPosition() == END) play = false, layer = 1, OLED_print();
          }
        }
    
        if (millis() - print_timer > 50){
          OLED_print();
          print_timer = millis();
        }
      break;

      //Time Lapse
      case 1:
        if (!run_cont) {
          if (direction && frame_count == 0) play = false, layer = 1, OLED_print();
          if (!direction && frame_count == max_frame) play = false, layer = 1, OLED_print();
        }
        if (frame_count == max_frame) direction = 1;
        else if (frame_count == 0) direction = 0;
        driver.shaft(direction);
        
        
        if (millis() - TL_timer >= TL_pause * 1000) {
          if (direction) stepper->moveTo(stepper->getCurrentPosition() - TL_steps, 1), frame_count--;
          else stepper->moveTo(stepper->getCurrentPosition() + TL_steps, 1), frame_count++;
          TL_timer = millis();
          
          /** CORRECT WITHOUT DELAY*/
          digitalWrite(33, HIGH);
          delay(50);
          digitalWrite(33, LOW);
          /** CORRECT WITHOUT DELAY*/
          
          if (debugM) Serial.print("max_frame ");
          if (debugM) Serial.println(max_frame);
          if (debugM) Serial.print("frame_count ");
          if (debugM) Serial.println(frame_count);
        }
      break;

      //Stop Motion
      case 2: 
        if (frame_count == max_frame) direction = 1;
        else if (frame_count == 0) direction = 0;
        driver.shaft(direction);

        if (playSel == 2) {
          if (direction == 1 && stepper->getCurrentPosition() - TL_steps >= HOME) {
            stepper->moveTo(stepper->getCurrentPosition() - TL_steps, 1), frame_count--;
            digitalWrite(33, HIGH);
            delay(50);
            digitalWrite(33, LOW);
          }
          else if (direction == 0 && stepper->getCurrentPosition() + TL_steps <= END) {
            stepper->moveTo(stepper->getCurrentPosition() + TL_steps, 1), frame_count++;
            digitalWrite(33, HIGH);
            delay(50);
            digitalWrite(33, LOW);
          }
          else temp_print();
        }
        else if (playSel == 1) {
          direction = !direction;
          driver.shaft(direction);
          if (!last_direction == 1 && stepper->getCurrentPosition() - TL_steps >= HOME) {
            stepper->moveTo(stepper->getCurrentPosition() - TL_steps, 1), frame_count--;
            digitalWrite(33, HIGH);
            delay(50);
            digitalWrite(33, LOW);
          }
          else if (!last_direction == 0 && stepper->getCurrentPosition() + TL_steps <= END) {
            stepper->moveTo(stepper->getCurrentPosition() + TL_steps, 1), frame_count++;
            digitalWrite(33, HIGH);
            delay(50);
            digitalWrite(33, LOW);
          }
          else temp_print();
          direction = !direction;
          driver.shaft(direction); 
        }
        last_direction = direction;
        play = false;
        
      /*  for PCB with direction pin
       *   
        if      (playSel == 2) {                           //next
          if (direction == 0) stepper->moveTo(stepper->getCurrentPosition() + TL_steps), frame_count++;
          else stepper->moveTo(stepper->getCurrentPosition() - TL_steps), frame_count--;
          //else temp_print();
        }
        else if (playSel == 1) {                           //prev
          if (direction == 1) stepper->moveTo(stepper->getCurrentPosition() + TL_steps), frame_count++;
          else stepper->moveTo(stepper->getCurrentPosition() - TL_steps), frame_count--;
        }

        digitalWrite(33, HIGH);
        delay(50);
        digitalWrite(33, LOW);
        play = false;
        
        */
        
      break;

      //Setting menu
      case 3:
//        direction = 0;
//        driver.shaft(direction);
//        stepper->moveTo(0, 1); 
      break; 
    }
  }

    if (stepper->getCurrentPosition() == stepper->targetPos() && menuList[functionMenuSel]->title != "Slider") {
      OLED_print();
    }

  
  if (menuList[3]->variables[2].val && layer == 1) {
  delay(500);
  direction = 0;
  driver.shaft(!direction);
  
  if (debugM) Serial.println(F("start homing"));
  homing();
  
  if (debugM) Serial.println(F("fine homing"));
  if (debugM) Serial.print(F("current Position: "));
  if (debugM) Serial.println(stepper->getCurrentPosition());

  assignVal();
  delay(200);
  
  stepper->setAcceleration(1000);
  stepper->setSpeedInUs(600); 
  direction = 1;
  driver.shaft(direction);
  stepper->moveTo(HOME, 1);
  Settings.variables[2].val = 0;
  
  if (debugM) Serial.print(F("steps tot: "));
  if (debugM) Serial.println(END);
  if (debugM) Serial.print(F("lunghezza loop: "));
  if (debugM) Serial.println(Settings.variables[0].val);

  double temp = Settings.variables[0].val;
  char txString[8];
  dtostrf(temp, 1, 2, txString);

  }
  
}

void temp_print() {
  display.clear();
  display.setTextAlignment(TEXT_ALIGN_CENTER);
  display.drawString(128/2, 64/2, "LOOP ENDED");
  display.display();
  play = false;
  delay (1000);
  OLED_print();
}

void firmware_update() {
  WiFi.mode(WIFI_STA);
  WiFi.begin(ssid, password);
  if (debugM) Serial.println("");

  // Wait for connection
  while (WiFi.status() != WL_CONNECTED) {
    delay(500);
    if (debugM) Serial.print(".");
  }
  
  if (debugM) Serial.println("");
  if (debugM) Serial.print("Connected to ");
  if (debugM) Serial.println(ssid);
  IP_address = WiFi.localIP().toString();
  if (debugM) Serial.print("IP address: ");
  if (debugM) Serial.println(IP_address);

  server.on("/", HTTP_GET, [](AsyncWebServerRequest *request) {
    request->send(200, "text/plain", "Welcome to AF.Slider firmware update page! Please go to yourIPaddress/update");
  });

  AsyncElegantOTA.begin(&server);    // Start AsyncElegantOTA
  server.begin();
  if (debugM) Serial.println("HTTP server started");

}
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

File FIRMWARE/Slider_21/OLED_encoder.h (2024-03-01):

//#include <Wire.h>               // Only needed for Arduino 1.6.5 and earlier
#include "SSD1306Wire.h"        // legacy: #include "SSD1306.h"
#include <SH1106.h>
#include "myfont.h"
//#include "EEPROM.h"
#include "TMC220xStepper.h"

#define SW 25 //4
#define DT 26 //2
#define CLK 27 //15

SH1106 display(0x3c, SDA, SCL);   

bool    isConnected = false;
String  caseSel = "";
int     input_speed = 100; // (mm/s)
double  input_acc = 2; // (s) - acelleration total time 
double  input_step = 10; //step for TM and SM (mm)
double  last_inputStep = input_step;
double  TL_pause = 2; //puase between steps fot TM and SM (s)
int     frame_count = 0; //counter to keep track for TM and SM
int     last_direction;
int     input_loop ;
int     input_startPoint;
int     max_frame;  //maximum number of shoot that can be taken
String  IP_address = "00:00:00:00";
bool    start_wifi = false;
bool    goingHome = false;
bool    revaluate = false;

volatile int lastEncoded = 0;
//long lastencoderValue = 0;
int lastMSB = 0;
int lastLSB = 0;

volatile bool updateData = true;
volatile unsigned long timing = 0; //timer generico per encoder
unsigned long firstPress = 0; //timer per pressButton
String lastFunction;

int8_t layer = 0;
int8_t functionMenuSel;
int8_t subMenuSel;
int8_t playSel;
int8_t valueSel;
volatile int8_t sumVal;

typedef struct subMenu{
  String title;     //name of the variable
  double multi = 1; //multiplier to obtain the basic unit (for example 1 for the step - integer - and 0.1 for the time - double)
  double val;       //variable value
  double maxVal;    //variable max value
  double minVal;    //variable min value
  String unit;      //variable dimension unit
};

typedef struct functionMenu{
  String title;
  subMenu variables[5];
};

functionMenu Slider;
functionMenu TimeLapse;
functionMenu StopMotion;
functionMenu Settings;

functionMenu *menuList[4] = { &Slider, &TimeLapse, &StopMotion, &Settings};



void OLED_print(){

  /*
   * Layer 0 --> main menu
   *  Layer 1 --> single function menu (slider, timelapse, etc)
   *  Layer 2 --> variable value selection
   *    Layer 3 --> "play" screen
   */
  
  display.clear();
  int lineSpace = 24;

    if(layer == 0){                                                       //print first layer menu 
      display.setTextAlignment(TEXT_ALIGN_LEFT);
      for (int i; i<4; i++){
        display.drawString(12, (i*16), menuList[i]->title );              // (x pos, y pos, string) --> text align set the distribution of the text starting from the x pos
      }
      display.drawString(0, (functionMenuSel*16), ">" );
    }

    if(layer == 1 || layer == 2){                                          //print second layer menu 
      if (menuList[functionMenuSel]->title != "Settings"){                 //print any sub menu except the "settings" sub menu
        display.setTextAlignment(TEXT_ALIGN_LEFT);
        for (int i; i<3; i++){
          display.drawString(12, (i*lineSpace), menuList[functionMenuSel]->variables[i].title ); //print varaible names 
          if (menuList[functionMenuSel]->variables[i].val != -1){     //print progress bar and value if required
            display.setTextAlignment(TEXT_ALIGN_RIGHT); 
            display.drawString(128, (i*lineSpace), (String)(menuList[functionMenuSel]->variables[i].val + menuList[functionMenuSel]->variables[i].unit));  
            display.setTextAlignment(TEXT_ALIGN_LEFT);
            double progress = (menuList[functionMenuSel]->variables[i].val / menuList[functionMenuSel]->variables[i].maxVal ) * 100;
            display.drawProgressBar(12, ((i*lineSpace)+15), 112, 8, progress);
          }
          
        }
        if (layer == 1) display.drawString(0, (subMenuSel*lineSpace), ">"); //print "inactive" cursor 
        else  {                                                             //print "active" cursor
          display.setFont(Roboto_Bold_12);
          display.drawString(0, (subMenuSel*lineSpace), "*"); 
          display.setFont(Roboto_Light_12);
        }

          if (subMenuSel == 3) display.setFont(Roboto_Bold_12);
          display.setTextAlignment(TEXT_ALIGN_RIGHT);
          display.drawString(126, 2*lineSpace, menuList[functionMenuSel]->variables[3].title);
          display.setTextAlignment(TEXT_ALIGN_LEFT);
          display.setFont(Roboto_Light_12);

      }
      
      else {                                                                //print "settings" sub menu
        display.setTextAlignment(TEXT_ALIGN_LEFT);
        lineSpace = 12;
        for (int i; i<5; i++){
          display.drawString(12, (i*lineSpace), menuList[functionMenuSel]->variables[i].title + menuList[functionMenuSel]->variables[i].unit); 
          
          if (menuList[functionMenuSel]->variables[i].title != "Back"){
            if (menuList[functionMenuSel]->variables[i].title == "Loop"){ 
              display.setTextAlignment(TEXT_ALIGN_RIGHT); 
              display.drawString(128, (i*lineSpace), (String)((int)menuList[functionMenuSel]->variables[i].val) );  
              display.setTextAlignment(TEXT_ALIGN_LEFT);
            }
            else if (menuList[functionMenuSel]->variables[i].title != "Firmware update"){    
              if (menuList[functionMenuSel]->variables[i].val) display.setTextAlignment(TEXT_ALIGN_RIGHT), display.drawString(128, ((i*lineSpace)), "ON"), display.setTextAlignment(TEXT_ALIGN_LEFT);
              else display.setTextAlignment(TEXT_ALIGN_RIGHT), display.drawString(128, ((i*lineSpace)), "OFF"), display.setTextAlignment(TEXT_ALIGN_LEFT);       
            }
          }
        }
        if (layer == 1) display.drawString(0, (subMenuSel*lineSpace), ">");   //print "inactive" cursor on layer 1
        else  {                                                               //print "active" cursor on layer 2
          display.setFont(Roboto_Bold_12);
          display.drawString(0, (subMenuSel*lineSpace), "*"); 
          display.setFont(Roboto_Light_12);
        }
        lineSpace = 24;
      }
    }
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

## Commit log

2023-04-06 Board added
    [copper_bottom.gbr, copper_top.gbr, drill_1_16.xln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]
2023-04-07 Added CAD data
    [Assieme Slider V3.4 v84.step]
2023-04-08 BOM & sourcing list added
2023-07-13 Added debug mode
    Added parameter DebugM to enable/disable serial.print

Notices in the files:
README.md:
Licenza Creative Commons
